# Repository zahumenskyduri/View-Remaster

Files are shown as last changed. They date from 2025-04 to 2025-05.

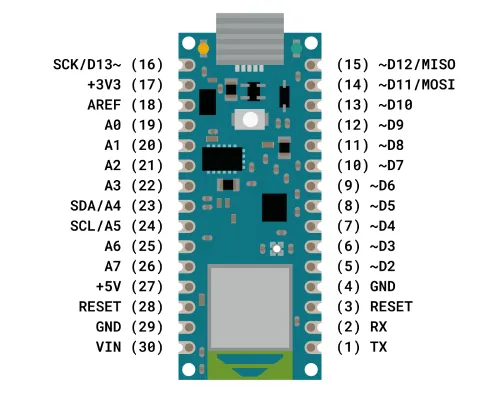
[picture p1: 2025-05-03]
HW pictures/arduino_nano_pinout.webp

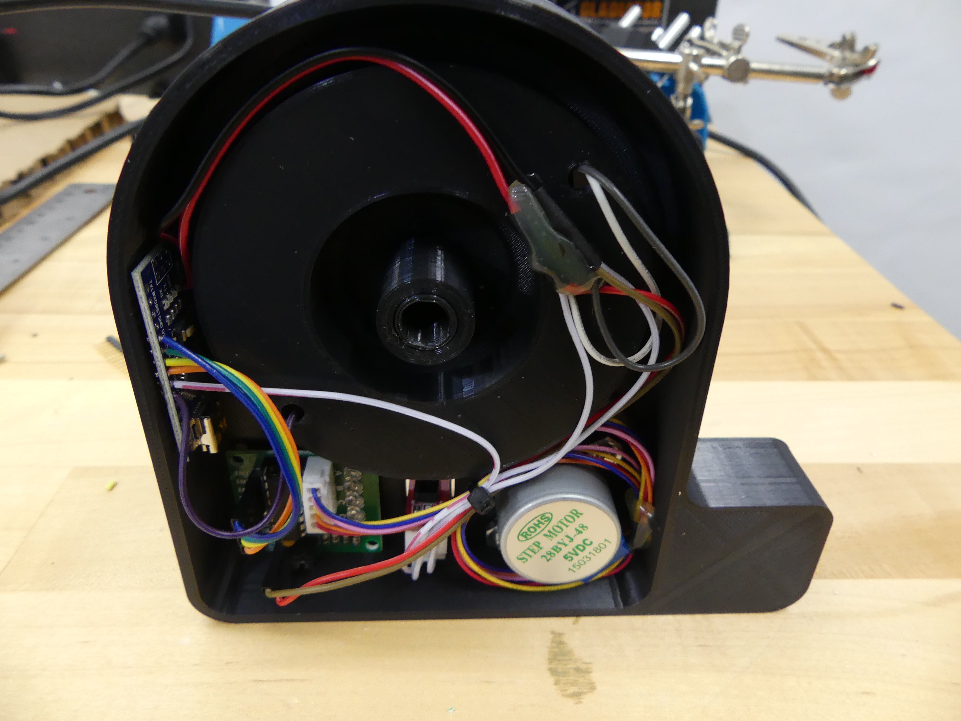
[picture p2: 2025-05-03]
HW pictures/4222051620428505859.JPG

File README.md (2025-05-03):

# View-Remaster
For this project, I made a View-Master Reel scanner.
I call it the View-Remaster. In short, this will scan in 3D View-Master reels and create a side-by-side (SBS) video that I can upload to YouTube.

I've been wanting to do this project for a VERY long time. So I'm excited to share it with you.

The channel that the video are uploading to are here:
https://www.youtube.com/channel/UCOirfwqCtgHvdcQz5gyFoTg

The build video is here:
https://youtu.be/6Y3vohi8WqI

# EDITS:

List of materials:

Bearing MF115ZZ:
https://www.aliexpress.com/item/1005007978162977.html

Google cardboard googles:
https://www.aliexpress.com/item/1005006466981096.html

Optical end stop sensor:
https://www.aliexpress.com/item/1005002219411174.html

Aluminium rod 12mmx300mm:
https://www.aliexpress.com/item/1005007360272645.html

Magnets 6x2mm:
https://www.aliexpress.com/item/1005008053185179.html

Motor 5V 4-Phase 28BYJ-48 DC Gear Step Stepper Motor+ULN2003 Driver Board:
https://www.aliexpress.com/item/1005006239720269.html

LED Adafruit Industries NeoPixel Jewel - 7 x 5050 RGBW LED w/Integrated Drivers
or alternative:
https://www.aliexpress.com/item/1005001693824089.html

         7 bit ws2812:
         https://www.aliexpress.com/item/1005007268165626.html or https://www.aliexpress.com/item/1005001693824089.html

         24 Leds ring
         https://www.aliexpress.com/item/1005002286128420.html

         Simple 3W 24mm Warm, no Wire
         https://www.aliexpress.com/item/1005006126055318.html

HD CS 5-50mm Varifocal Lens Industrial 30fps 4K 8MP CCD IMX415 USB Webcam:
https://www.aliexpress.com/item/1005008657226691.html

Extension tubes:
https://www.aliexpress.com/item/1005004909394341.html

MosFET trigger:
https://www.aliexpress.com/item/1005008217485311.html

Lamp:
https://www.aliexpress.com/item/1005003057943564.html

# Connection:

         VCC (5V) <> Led+
                  <> Sensor V
                  <> Stepper 5V+

         GND      <> LED-
                  <> Sensor G
                  <> Stepper 5V-

         Data ports:
         PD02     <> Stepper In1
         PD03     <> Stepper In2
         PD04     <> Stepper In3
         PD05     <> Stepper In4
         PD06     <> Sensor S
         PD07     <> LED in
         PD10     <> Lamp on/off
         PD11     <> Lamp light temperature

Untitled Diagram drawio

# STL Changes

ReelSupport v18

        Merged Reelsupport v17 with helical ring gear

Helical gear v3

        Separated helical gear

BearingHolder v5_MF115ZZ

        BearingHolder v4 adjusted for use with bearing MF115ZZ

MasterReelBase adjusted (v27)

        for use with bearing MF115ZZ
        7bit light (diameter 25mm)
        holes for M3 bolts
        seat for m3

Camera_base v4 and Camera_base_Reel v5

        holes for M3 bolts
        seat for m3

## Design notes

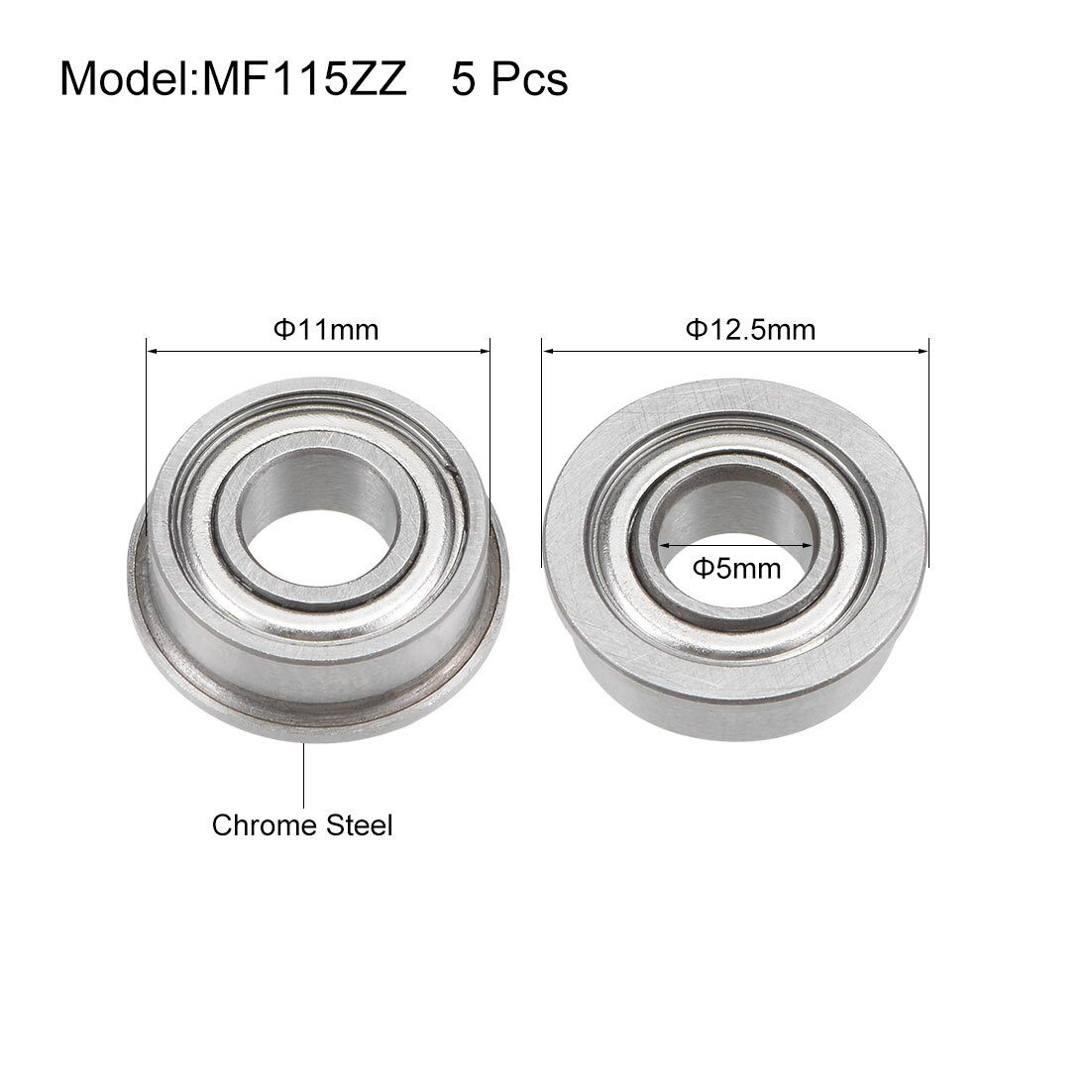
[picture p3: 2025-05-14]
HW pictures/bearing.jpg

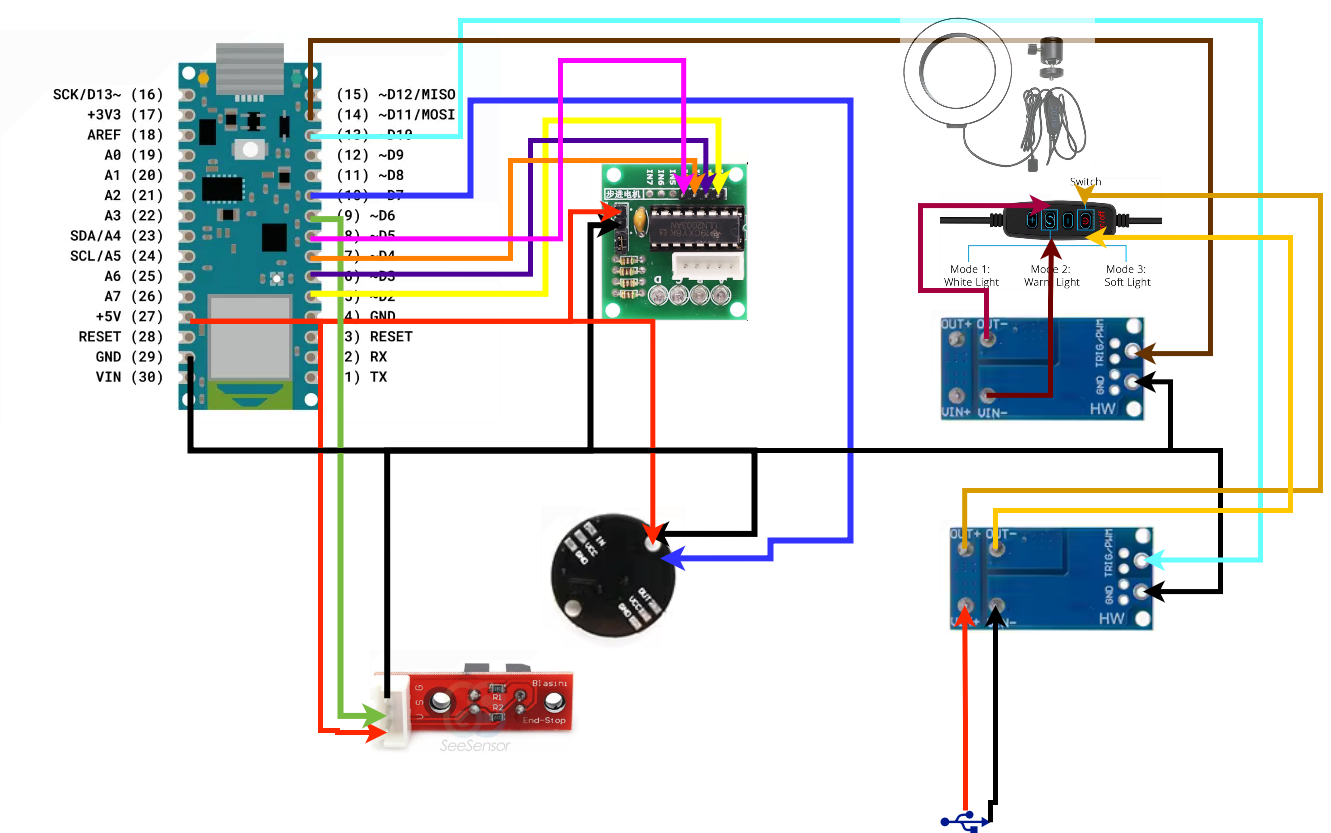
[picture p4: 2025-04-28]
Diagram/View-Remaster.drawio.png

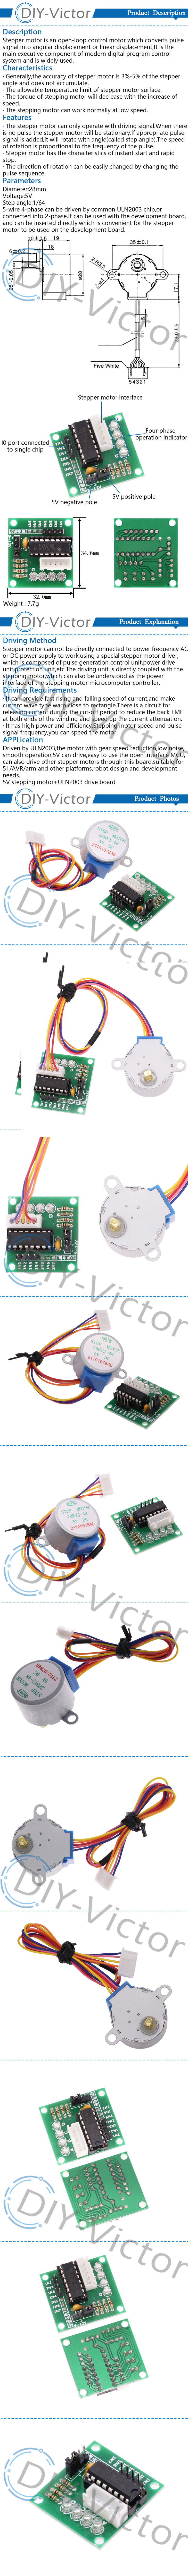
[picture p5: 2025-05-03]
HW pictures/S1d75822b252a4a999aaa790b7fb6eb0fF.jpg.jpeg

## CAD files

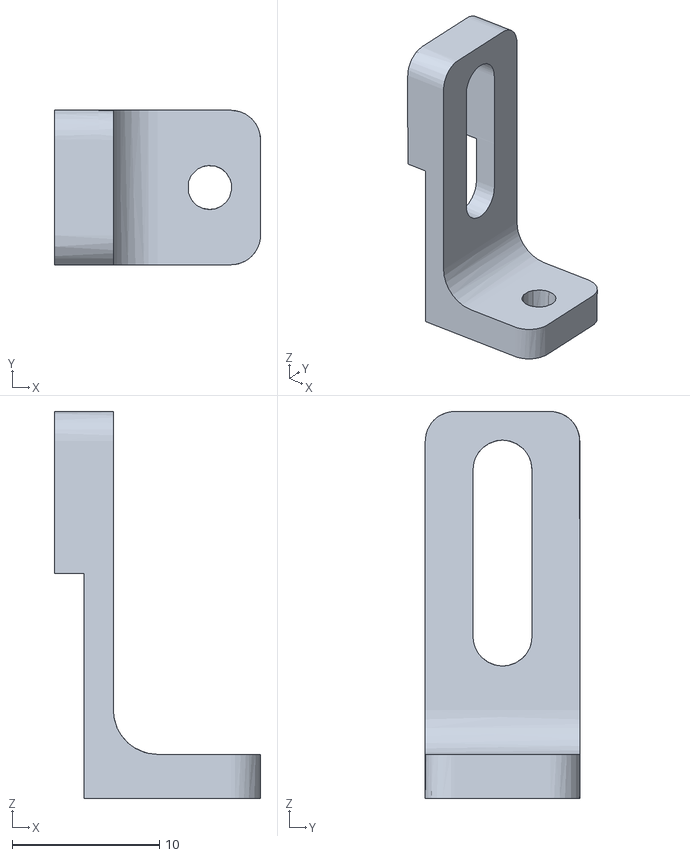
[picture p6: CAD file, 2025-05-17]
STL/SensorMount v9.stl
14.0 x 10.5 x 26.3

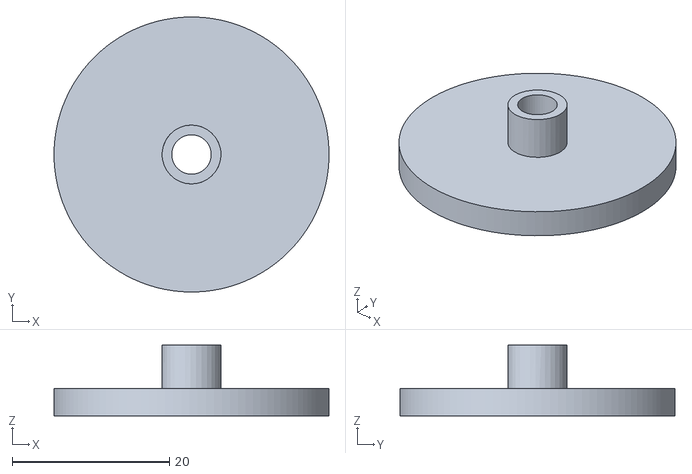
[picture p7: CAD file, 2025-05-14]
STL/ReelMount v8 m5.stl
35.0 x 35.0 x 9.00

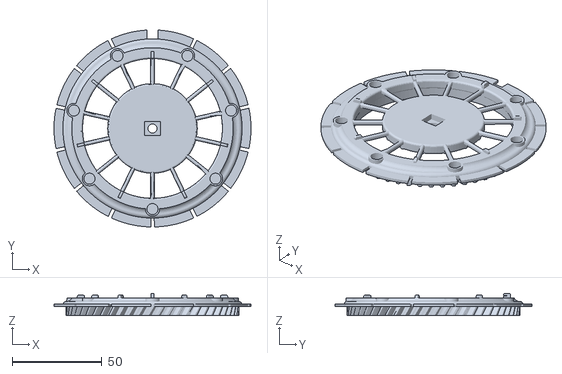
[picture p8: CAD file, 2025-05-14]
STL/ReelSupport v19 m5.stl
110.0 x 109.9 x 12.5

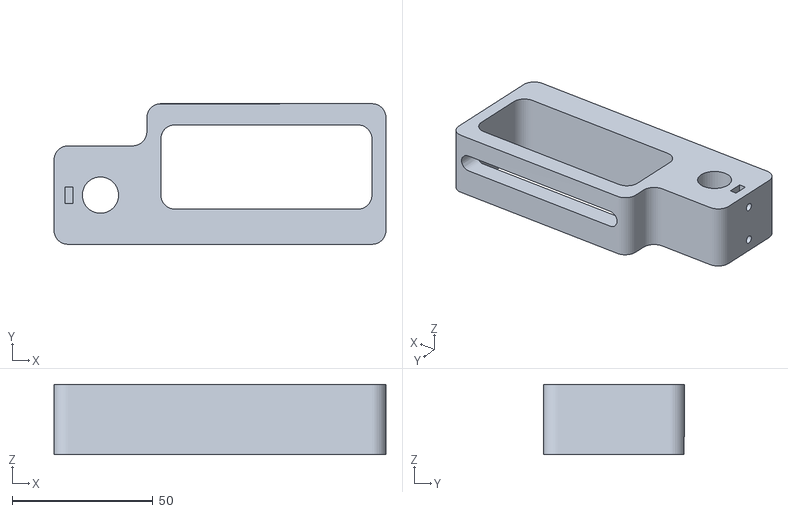
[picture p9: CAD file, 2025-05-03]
STL/Camera_base_Reel v5.stl
118.0 x 50.0 x 25.0

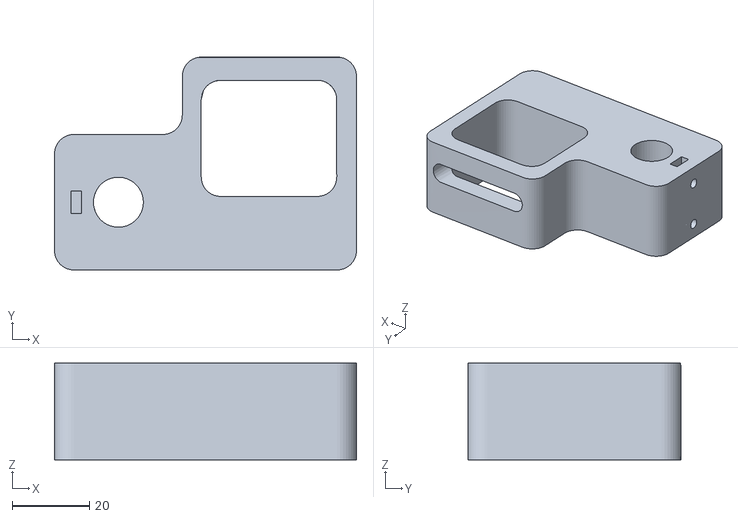
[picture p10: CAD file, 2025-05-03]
STL/Camera_base v4.stl
78.0 x 55.0 x 25.0

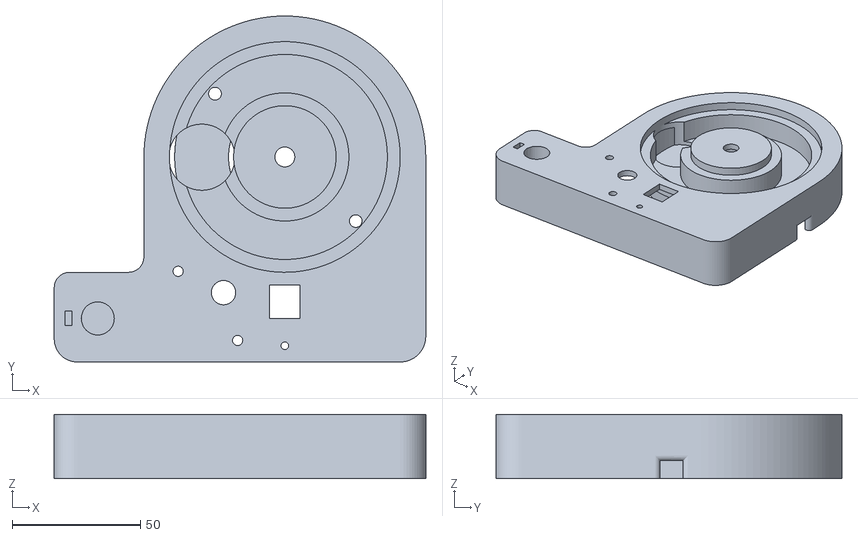
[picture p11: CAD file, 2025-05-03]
STL/MasterReelBase v27_MF115ZZ.stl
145.0 x 135.0 x 25.0

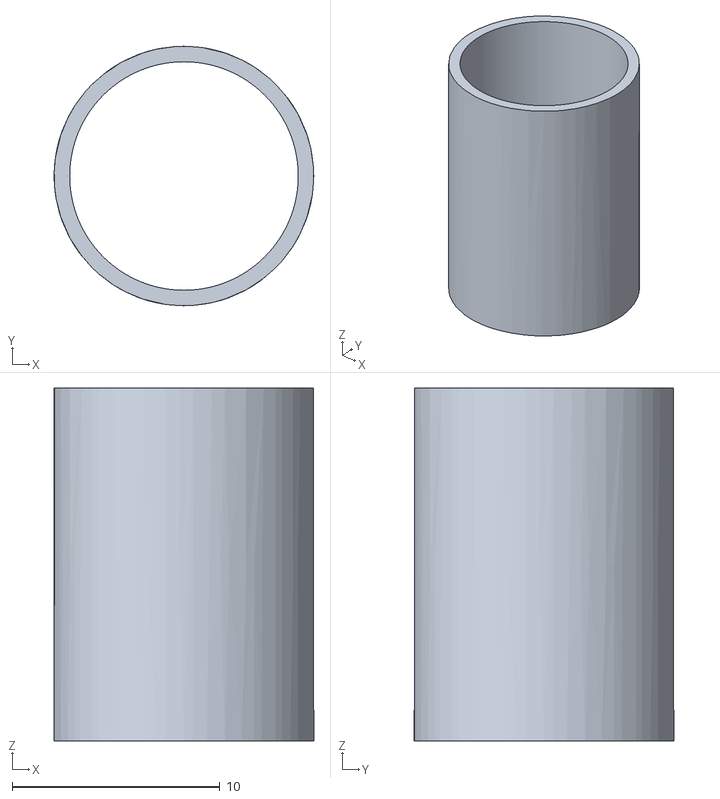
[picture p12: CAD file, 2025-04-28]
STL/BearingHolder v5_MF115ZZ.stl
12.5 x 12.5 x 17.0

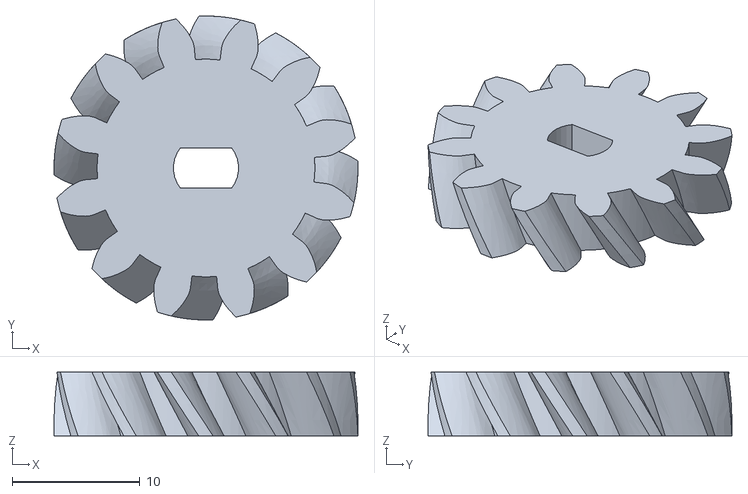
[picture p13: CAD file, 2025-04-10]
STL/helical gear v3.stl
23.8 x 23.8 x 5.00

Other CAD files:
STL/ReelSupport v18.stl

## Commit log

2025-04-10 Update README.md
    added list of materials
    STL changes
2025-04-10 Add files via upload
    merged reelsupport with helical ring gear
    separated helical gear into single file
    [ReelSupport v18.stl, helical gear v3.stl]
2025-04-28 Add files via upload
    adjusted to use with bearing MF115ZZ
    [BearingHolder v5_MF115ZZ.stl]
2025-04-28 Add files via upload
    adjusted for use with bearing MF115ZZ
    [MasterReelBase v24_MF115ZZ.stl]
2025-05-02 Add files via upload
    adjusted to use with m5 bolt
    [MasterReelBase v26_MF115ZZ.stl]
2025-05-03 Add files via upload
    adjusted for m3 screw and added pocket for m3 nut
    [Camera_base v4.stl, Camera_base_Reel v5.stl, MasterReelBase v27_MF115ZZ.stl]
2025-05-03 sync
    adjustments
    [BearingHolder v4.stl, Camera_base v3.stl, Camera_base_Reel v4.stl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]
2025-05-14 updates
    bearing picture
    updates to stl to fit m5 screw
    [ReelMount v8 m5.stl, ReelSupport v19 m5.stl]
2025-05-17 Create SensorMount v9.stl
    [SensorMount v9.stl]
